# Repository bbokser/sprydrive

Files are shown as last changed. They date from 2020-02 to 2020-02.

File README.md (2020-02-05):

# sprydrive

SpryDrive is an affordable actuator based on the quasi-direct drive (QDD) scheme. It is composed of a brushless outrunner motor, a low-cost metal gearbox, and a 3D-printed housing. Inspired by Gabrael Levine's OpenTorque actuator, but takes up less volume.

Output Backlash: ~0.13 degree  
Gear Ratio: 7:1  
Motor: Herlea X8318S or Turnigy 9235

The 8318 motor and 9235 motor are nearly identical, but the 8318 is 2.5 mm longer, so there are two versions of the design. Keep this in mind when ordering parts.

## Instructions

### Useful Tools

1. Hex key set
2. Arbor press
3. Milling machine with end mill (Don't worry, this is for a very easy, simple facing operation).
4. 400 grit sandpaper
5. Electric drill
6. M4 tap
7. Glue stick
8. A 3D printer and nylon, ABS, or PLA filament. I recommend Prusa.
9. Micrometer

### Steps

*Pictures coming soon!*

1. See SpryDrive BoM.xlsx for part sourcing. Order from McMaster if you're in a rush, order Aliexpress if you want to save money. Same thing with HobbyKing versus Alibaba/Aliexpress.

2. Submit LaserCut.DXF to SendCutSend.com for the aluminum Adapter Plate and Output Mounting Plate. Choose Aluminum 6061 (Not 5052) and a thickness of 0.125". I have included 6 copies of each component in the DXF because $29 is their minimum charge. If you want more, the best way to change this is to install something like [QCAD](https://qcad.org/en/) and duplicate outlines as needed.

4. Use an arbor press or vise to press out the dowel pins that come with the VersaPlanetary carrier plate. You will need a small piece of hardware to push directly on the pins, such as a smaller dowel pin. (Pictures coming soon).

5. The M4x18 dowel pins will replace the ones you just removed. You will need to sand the diameter down to achieve a proper press fit with the carrier plate. Mark off a 10 mm section of one end for sanding.

6. Insert the other end into an electric drill and hold a 400 grit sandpaper sheet around the 10 mm section while spinning the dowel pin at high speed. Measure the diameter with a micrometer every 30 seconds or so. The pin will start out at about 4.003 mm (.1576 in), and you want it to measure about 3.978 mm (.1566 in). This can take a few minutes. You wouldn't think taking off one thou would matter, but it means the difference betweeen a broken carrier plate and an easy press fit. I learned this the hard way!

7. Use an arbor press to insert the dowel pin into the VersaPlanetary carrier plate. The dowel pin should extend out 8 mm on one side and 5.3 mm on the other.

8. Repeat steps 5-7 for the other two dowel pins.

9. Tap the 3.5 mm holes in the laser cut Output Mounting Plate with an M4 tap.

10. Using an end mill, face the ring gear down by roughly 3.2±0.5 mm. Be sure to fixture this carefully, you don't want to deform it. The purpose of this operation is just to reduce the length of the actuator. If you want to skip this step, you can simply increase the length of the 3D-printed frame by 3.2 mm, but the sun gear will have less contact area with the planets.

11. 3D-print the Frame, Output Plate, Back Plate, Bearing Cover, Magnet Holder, and Encoder Mount. I used PLA, but you can use nylon, ABS, PETG, etc. Use 50% infill and at *least* 4 perimeters.

12. When printing the Output Plate, you must stop the print partway through to insert the bearing. It depends on your printer, but here is one [guide](https://www.youtube.com/watch?v=MfUjkI0ugX8). I recommend using a glue stick to help the rest of the print adhere to the bearing face.

13. Use a soldering iron to insert the heat-set inserts into the Frame.

14. Press the ring gear into the Frame.

15. Press the sun gear into the Adapter Plate. You may need an arbor press for this.

15. The rest of the assembly is easy and can be done using the assembly model as reference.

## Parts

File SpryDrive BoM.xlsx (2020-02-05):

Item Number | Part Name | Per Actuator | Order Quantity | Unit Cost | Total Cost | Source | Alternate Source | Alternate Source 2 (Unverified)
1 | X318S or 9235 Motor | x1 | 1 | $55 ~ $105.50 |  | https://www.alibaba.com/product-detail/X8318S-Electric-Brushless-Motor-For-RC_60743175936.html | https://hobbyking.com/en_us/9235-100kv-turnigy-multistar-brushless-multi-rotor-motor.html | https://www.aliexpress.com/item/32980862851.html
2 | Frame | x1 | 1 | Filament |  | 3D Print - Nylon, ABS, or PLA
3 | Output Plate | x1 | 1 | Filament |  | 3D Print - Nylon, ABS, or PLA
4 | Back Plate | x1 | 1 | Filament |  | 3D Print - Nylon, ABS, or PLA
5 | Bearing Cover | x1 | 1 | Filament |  | 3D Print - Nylon, ABS, or PLA
6 | Magnet Holder | x1 | 1 | Filament |  | 3D Print - Nylon, ABS, or PLA
7 | Encoder Mount | x1 | 1 | Filament |  | 3D Print - Nylon, ABS, or PLA
8 | Output Mounting Plate | x1 | 1 | $29.00 | $29.00 | Sendcutsend.com
9 | Adapter Plate | x1
10 | M4x10 Flat Head Screws (Steel) | x4 | 1 | $1.37 | $1.37 | https://www.aliexpress.com/item/32964226154.html | https://www.mcmaster.com/91294a190
11 | M2x10 Flat Head Screws (Steel) | x16 | 1 | $1.82 | $1.82 | https://www.aliexpress.com/item/32964226154.html | https://www.mcmaster.com/91294a006
12 | M3x8 Ultra-Low Profile Socket Head Screws | x4 | 1 | $2.37 | $2.37 | https://www.aliexpress.com/item/4000231097606.html | https://www.mcmaster.com/90358a002
13 | M4x18 Dowel Pins | x3 | 1 | $5.79 | $5.79 | https://www.mcmaster.com/93600a455
14 | M2 Brass Heat-Set Inserts | x12 | 1 | $8.79 | $8.79 | https://www.mcmaster.com/94459a110 |  | https://www.aliexpress.com/item/4000232526110.html
15 | M2.5 Thin Hex Nuts | x4 | 1 | $2.35 | $2.35 | https://www.mcmaster.com/90710a025 | https://www.aliexpress.com/item/32895301400.html
16 | M4 Hex Nuts (Optional For Mounting) | x4 | 1 | $1.41 | $1.41 | https://www.mcmaster.com/90592a090
17 | Deep Groove Bearing 40x52x7 | x1 | 1 | $19.49 | $19.49 | https://www.vxb.com/6808-2RS-Bearing-Deep-Groove-6808-2RS-p/6808-2rsbearing.htm
18 | AS5048 Encoder Board and Magnet | x1 | 1 | $16.76 | $16.76 | https://www.digikey.com/product-detail/en/ams/AS5048A-TS_EK_AB/AS5048A-AB-1.0-ND/3188612
19 | VersaPlanetary 7:1 Gear Set | x1 | 1 | $14.99 | $14.99 | https://www.vexrobotics.com/versaplanetary.html
20 | VersaPlanetary Ring | x1 | 1 | $9.99 | $9.99 | https://www.vexrobotics.com/217-2816.html
 | TOTAL |  |  |  | $114.13 | Total does not include motor, 3D printing costs, and shipping.

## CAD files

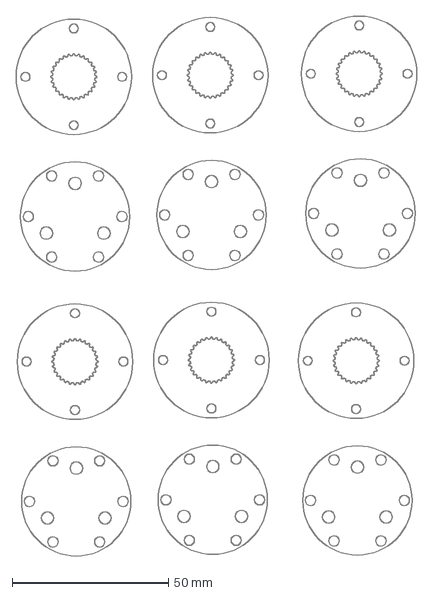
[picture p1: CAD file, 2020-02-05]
LaserCut.dxf
128.4 x 173.0 mm

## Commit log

2020-02-05 Added instructions, BOM, and LaserCut.DXF
    [LaserCut.dxf, SpryDrive BoM.xlsx]
2021-04-21 Fixed error in motor axial lengths (and frame axial lengths as a result)
